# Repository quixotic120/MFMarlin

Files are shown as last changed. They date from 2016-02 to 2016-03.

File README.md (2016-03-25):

# MFMarlin
Marlin 1.1.0 RC3 for Makerfarm Pegasus

**in this configuration software endstops are turned off; as a result you will be able to crash the head very easily if you manually move the print head or incorrectly set offsets. If you do not want it to act this way edit line 404 of configuration.h to be true instead of false**

newest changes: speed has been changed because I changed my stepper drivers. I blew out the stepsticks that came with it because I am dumb and replaced with DRV8825 - trying out 1/32nd stepping for now. Added in second extruder but recently picked up a diamond hotend - added experimental support for CMY color mixing. Untested.

added a ferrite core to the servo signal line and powered with a 7805 rather than using the arduino. Jitter is improved quite a bit but still present unfortunately. Considering building a [noise trap](http://www.sentex.ca/~mec1995/gadgets/noiserx.htm) because I found a hex-schmitt IC in my parts bin; also might add caps to the power and signal lines (see arduino_servo_filters.jpg)

https://github.com/MarlinFirmware/Marlin - I didn't fork because I'm dumb but all the real work is from here; mine is merely a configuration for a 10" Makerfarm pegasus, figured I would share to help anyone else that has a similar setup. I'm also using this document as a collection of what I've done so I can keep track.

This is typically going to be configured for my setup (described below). I'll try to maintain it for as long as possible but no guarantees on that front. I would suggest that if you download this you read over configuration.h at least once - you'll likely at least need to change the bed size and would probably benefit from adding your own PID tunings. If you are using auto bed level you will need to enter the measurements for your machine and if not you should disable it and turn software endstops on.

I have a 10" Pegasus dual extruder with E3Dv6 extruders, graphical LCD, a servo for auto bed leveling (abl), 3mm Borosilicate over bed, SSR on bed for PID control, new bed clips, and some other mods that don't impact the firmware (octopi, cooling for Ramps, lighting, etc). Working fine for me however I do not take any responsibility for you destroying your machine or whatever and no warranty is expressed or implied. Also - I tend to err on the side of slower printing so you may need to play with that a bit for your preferences.

my current slicer settings posted in /slicer as an fff file for simplify3d. If you don't use S3D you can just open it on github; it's basically an XML file. I typically end up messing with the standard stuff, infill/raft/layer height/temperature/etc but the rest is mostly locked in at this point.

Change notes for MFMarlin:
configuration.h

line 73: MB type; I have it set to BOARD_RAMPS_14_EEB - extruder, extruder, bed. Single extruder may want EFB at the end (extruder, fan, bed) or something else depending on what you have connected to D10/9/8, see 

line 78: custom machine name if you want to change the "pegasus ready" text

line 86: define # of extruders. set to 1 currently because I broke my secondary thermistor. D'oh!

thermal settings should be the same unless you've changed thermistors. On that note I've read Makerfarm uses custom thermistor tables but I compared his versus the one in this release and they were essentially identical so thermistortables.h is unchanged; unsure if what I heard was wrong or if this only applies to the prusa i3v

lines 175-178 may have to change for E3Dv6 lite? 

PID:
lines 218-20 are the settings from my extruder with pidautotune, would probably be beneficial to run your own and put in your own values (M303 E0 C8 S210, where E is device (e0 ext 1, e1 ext 2, e-1 bed), C is # cycles, and S is target temp). I see that RC3 has the option to use seperate PID for each extruder, I will likely play with this some more when my replacement thermistor comes

line 246 (#define PIDTEMPBED) - comment this out if you do not use PID for the bed (if you are using the default relay from the kit you should comment this out, I use a Fotek SSR)

lines 270-72 are my bed settings from pidautotune, again suggest you grab your own (M303 E-1 C8 S100)

thermal runaway is on, settings for this have moved to configuration_adv.h - I upped the protection period to 60s because I found myself getting false positives with the PID bed. Consider changing configuration_adv.h line 21 to 40 if you are not. 

back to configuration.h:
346-52: endstop inverting. I have them all as false, colin's has x_max inverted which shouldn't matter as the machine doesn't have max endstops - on that note line 353 is not commented out, comment out to add max endstops 

404 - set to false, set to true if you aren't using abl/are using abl with a second endstop wired in series.

410-415 - my bed limits. If you have the 8" machine this will definitely need to be changed. If you have the default 10 with binder clips you'll probably have to pull it in a bit; I've modified how my glass clamps to the bed to maximize build area. I also place my x and y endstops at x0 y0

420 - filament runout sensor is commented out, not using.

430-50 manual bed leveling is commented out because I'm using abl, uncomment line 434 to add it back into the menu

auto bed level section

457 - comment out to disable ABL

480-83 - box, if you've changed the bed size you'll likely need to change this

489 - # of probe points x 3, set to 3 (probes 9 points)

506-08 - z probe offsets from extruder - [you will need to measure these on your own] (http://zennmaster.com/random-things/auto-bed-leveling-for-the-makerfarm-prusa-i3-part-3-final-setup)

510-517 - z probe behavior, customize to your preference

602-613 - copied from Colin's release. Ensure these values match the ones in your machines config, especially axis_steps_per_unit!

640 - eeprom storage enabled

654-61 - preheat settings. Mine are probably a touch high but they work for my primary filament brand (inland)

LCD - 
if you're using no LCD comment out line 725 (#define REPRAP_DISCOUNT_FULL_GRAPHIC_SMART_CONTROLLER). If you're using the graphic LCD leave as is and install the [u8glib arduino library](https://github.com/olikraus/u8glib)

if you're using the other LCD comment out 725 as above and I believe you uncomment line 715: #define REPRAP_DISCOUNT_SMART_CONTROLLER

RC servo stuff:
comment out line 816 to disable servos

if you are using a servo for abl ensure you set #define SERVO_ENDSTOP_ANGLES on line 826 for your setup

if the servo is unable to complete moves increase servo_activation_delay on line 837, I'm using a towerpro 9g servo so I had to up it a bit. If you notice the servo jerking a bit after it's finished you might need to decrease it. 

other changes:
ultralcd.cpp line 1669 - changed incrementor to += to invert direction of rotary knob on LCD display

bugs found:
random reboot - appears to be a function of using too much at once (e.g. ramping heat WAY up on both extruders and bed while having the carriage move around) and is most likely an issue with my power supply, but still trying to see if I can reproduce it. 
SD sometimes not detected after reboot - every time this has happened reseating the card has fixed the issue. again, trying to reproduce consistently. 

msg me if you find a bug or have questions although I do not guarantee I can help or will respond in a timely manner.

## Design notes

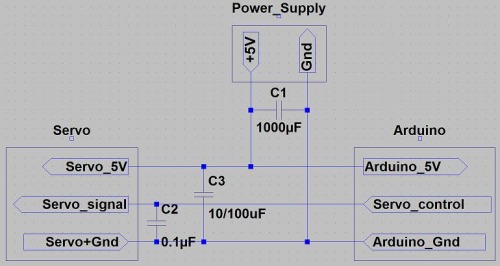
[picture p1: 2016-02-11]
Arduino_Servo_Filters.jpg

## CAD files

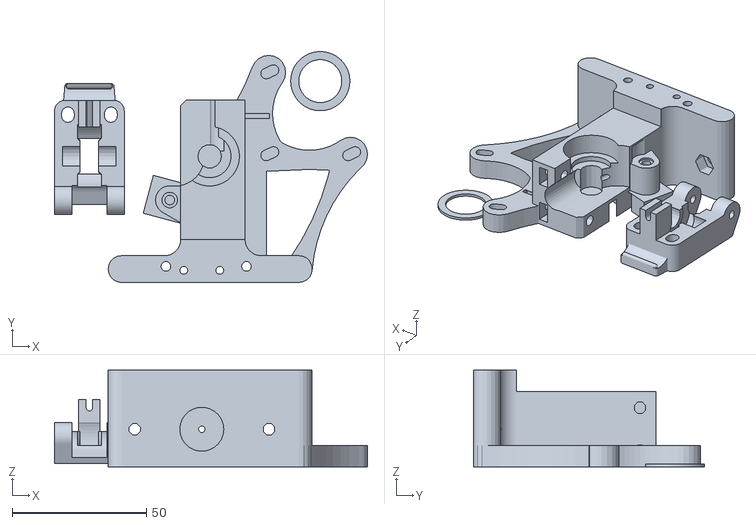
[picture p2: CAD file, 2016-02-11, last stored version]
mods/bowden/orig/ult-gregs-wades-30mm-v1_complete.stl
116.6 x 86.0 x 36.0

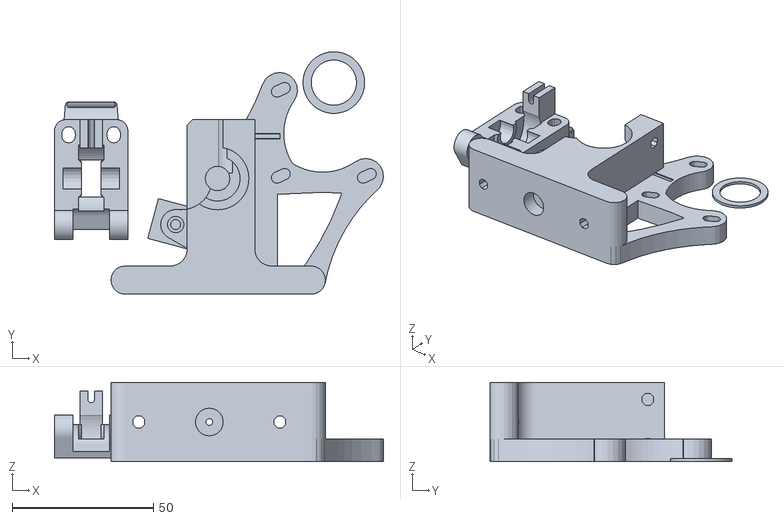
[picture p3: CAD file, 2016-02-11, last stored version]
mods/bowden/bowden mod/ult-gregs-wades-Bowden_base-v1.stl
116.6 x 85.9 x 28.0

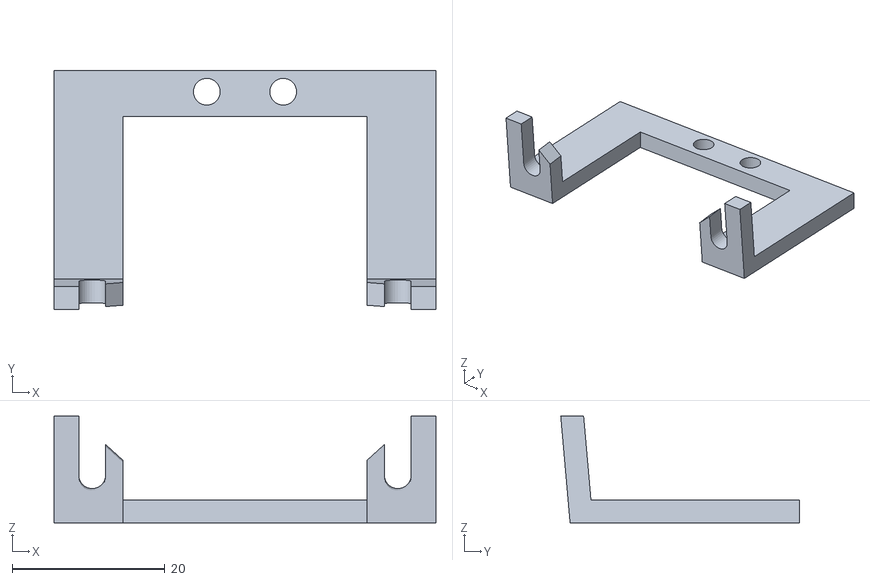
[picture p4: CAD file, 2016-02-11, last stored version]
mods/bowden/e3d mount/Bowden_carriage_clamp_50mmFanbracket.stl
50.0 x 31.2 x 14.0

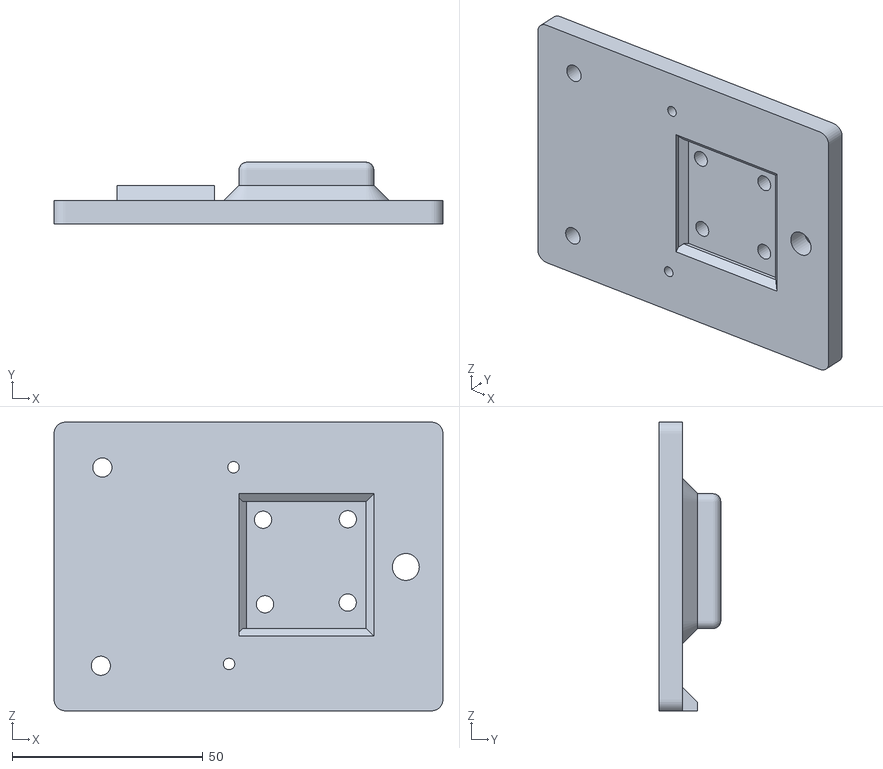
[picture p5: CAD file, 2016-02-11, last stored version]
mods/bowden/e3d mount/E3D_V6_Bowden_mount_with_servo./i3v_Conversion_bracket_1.stl
102.0 x 16.2 x 75.8

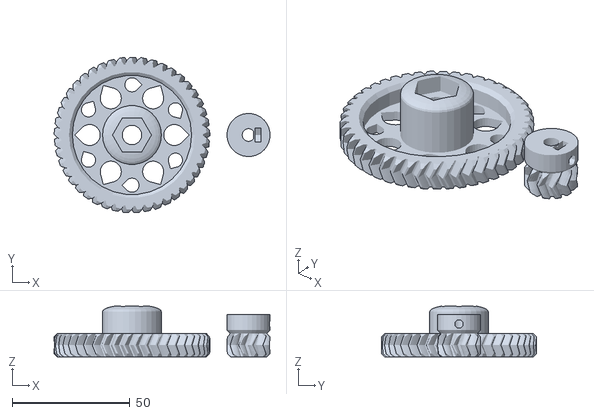
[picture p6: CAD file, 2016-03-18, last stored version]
mods/bowden/flexy mod w: bowden/WadeHerringboneGears.stl
91.7 x 65.9 x 21.6

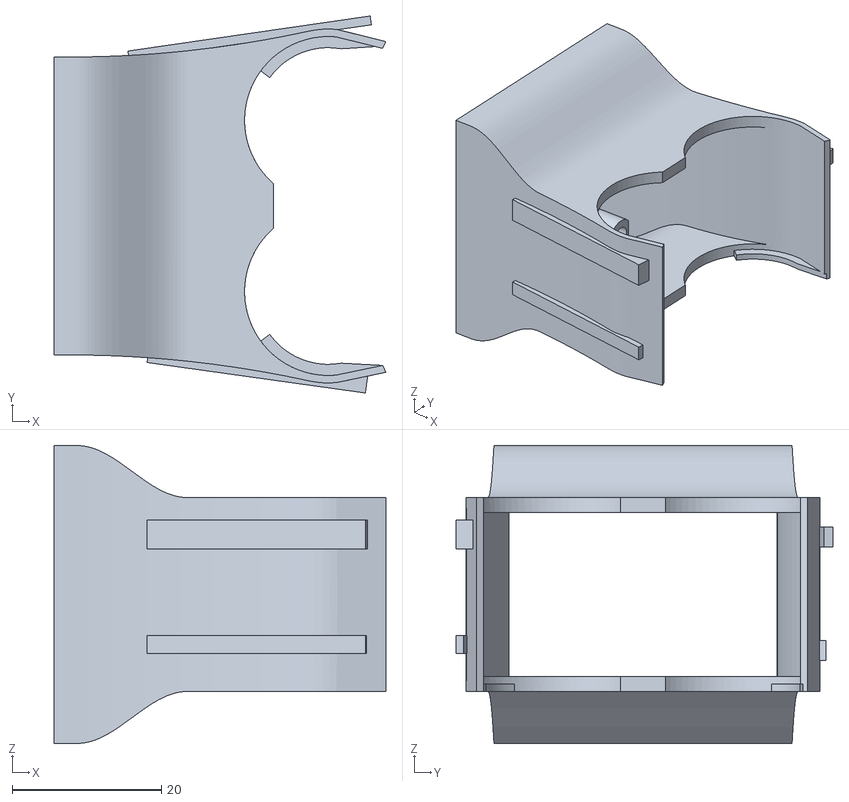
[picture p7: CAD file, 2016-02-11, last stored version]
mods/fan shroud/shroud.stl
44.5 x 50.6 x 40.0

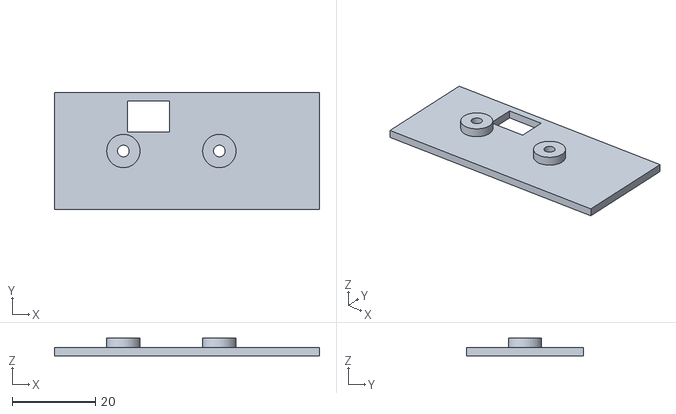
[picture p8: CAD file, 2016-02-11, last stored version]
mods/OrmerodSensorBoard/PrintedPartsForSensorBoard/Insulator-diff-led-dual-nozzle.stl
63.5 x 28.0 x 4.25

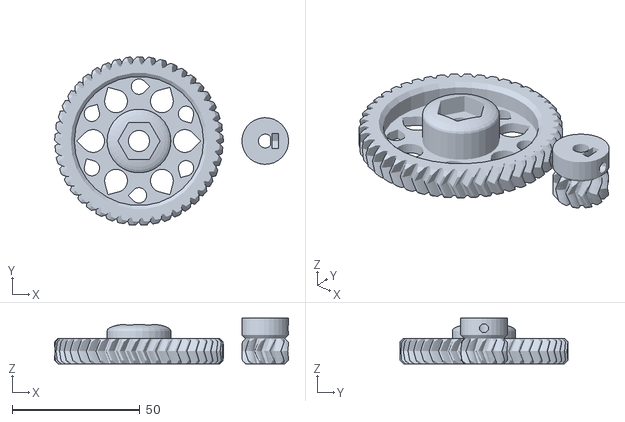
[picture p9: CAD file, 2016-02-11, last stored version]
mods/bowden/bowden mod/WadeHerringboneGears.stl
91.7 x 65.9 x 18.0

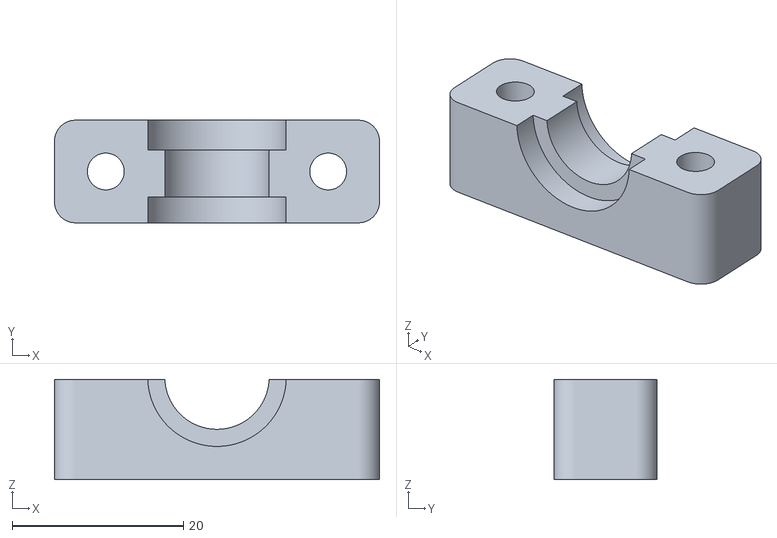
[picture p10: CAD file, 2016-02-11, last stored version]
mods/bowden/e3d mount/Bowden_carriage_clamp.stl
38.0 x 12.0 x 11.8

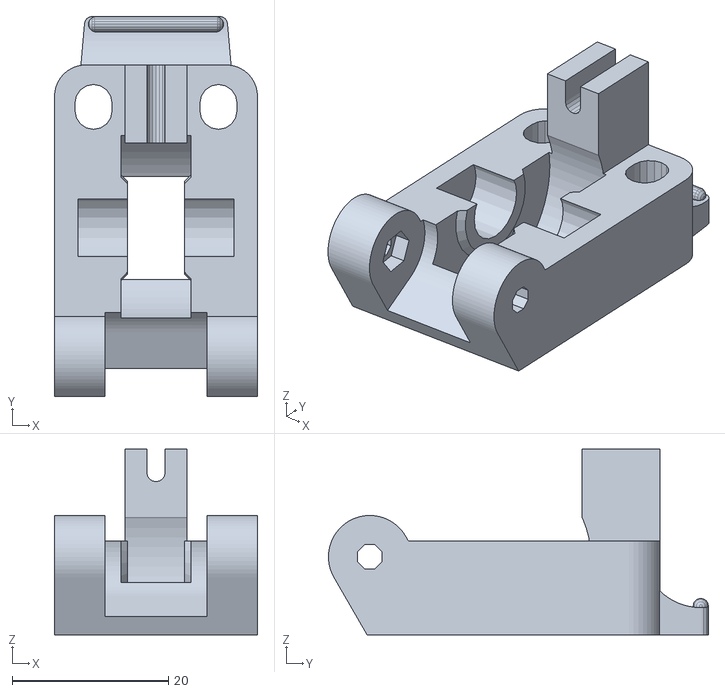
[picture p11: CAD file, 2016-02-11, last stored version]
mods/bowden/orig/ult-gregs-wades-30mm-v1_guidler.stl
26.0 x 48.7 x 23.8

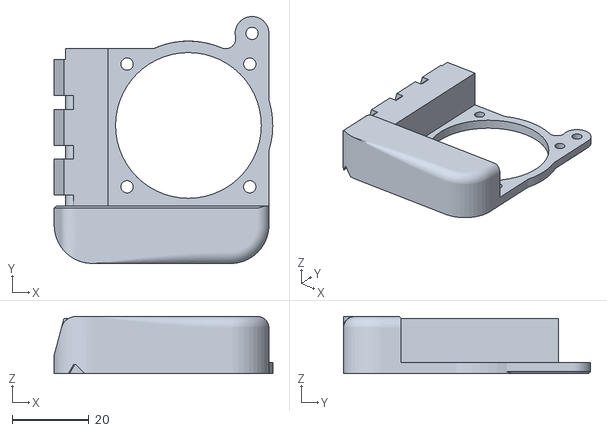
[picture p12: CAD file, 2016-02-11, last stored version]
mods/OrmerodSensorBoard/PrintedPartsForSensorBoard/original-rrp-fan-duct.stl
57.0 x 64.4 x 14.9

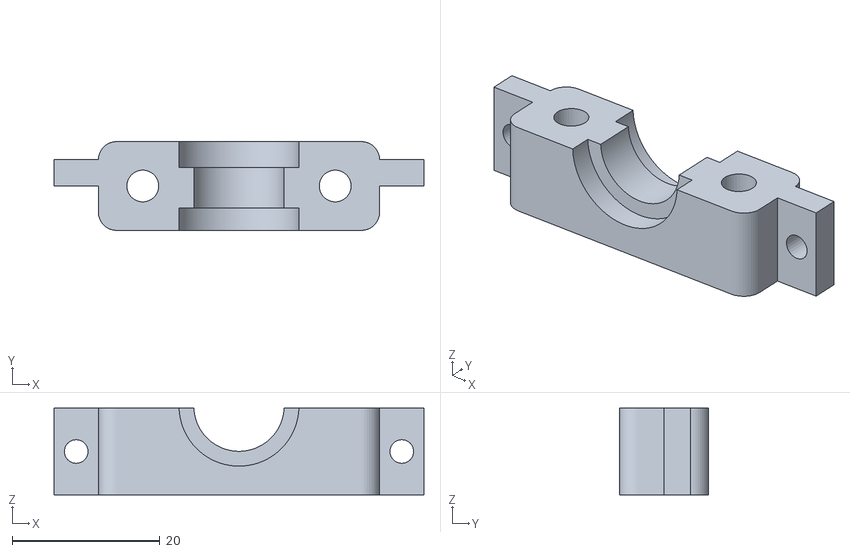
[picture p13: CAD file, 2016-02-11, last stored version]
mods/bowden/e3d mount/Bowden_carriage_clamp_FanMount.stl
50.0 x 12.0 x 11.8

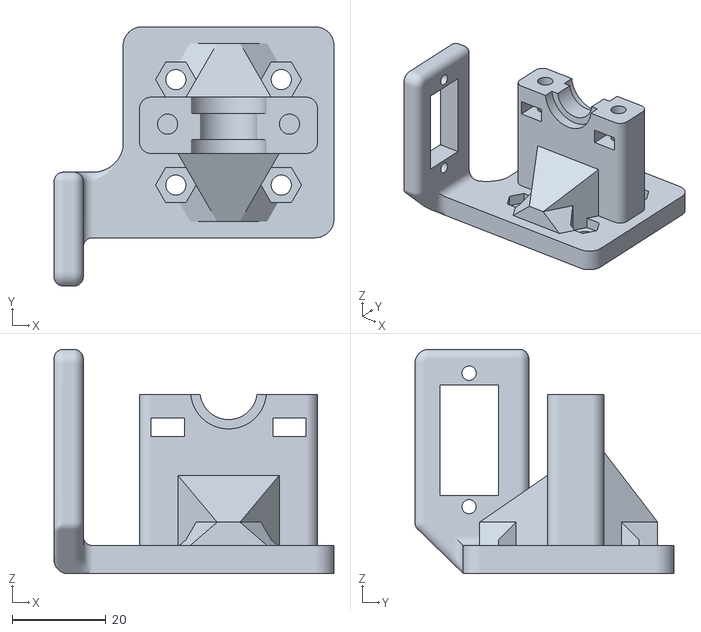
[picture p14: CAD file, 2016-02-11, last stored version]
mods/bowden/e3d mount/E3D_V6_Bowden_mount_with_servo./e3d_bowden_w_servo.stl
59.8 x 55.3 x 47.9

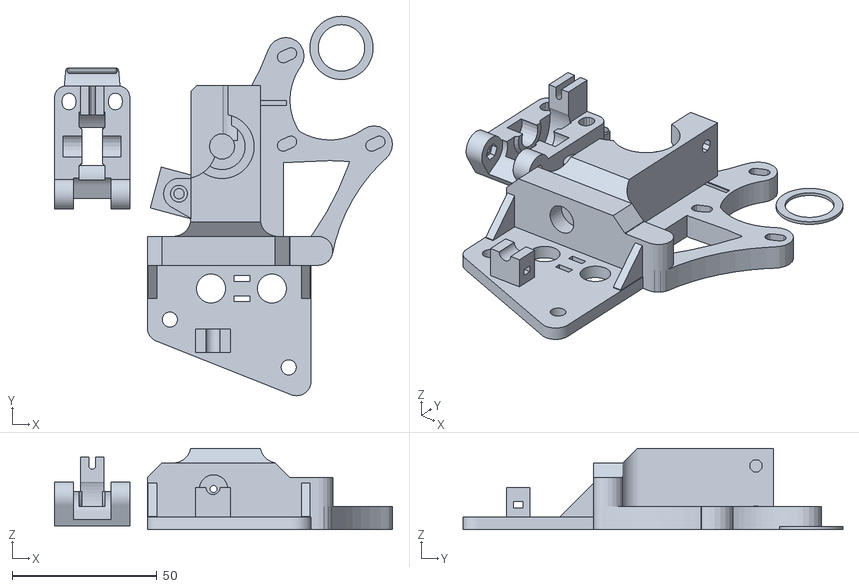
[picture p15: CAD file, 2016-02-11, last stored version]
mods/bowden/bowden mod/ult-gregs-wades-Bowden_bracket-v1.stl
116.6 x 130.9 x 28.0

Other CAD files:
mods/bowden/flexy mod w: bowden/flexy-fixed-gregs-wades.stl
mods/bowden/bowden mod/configuration.scad
mods/bowden/flexy mod w: bowden/configuration.scad
mods/bowden/orig/configuration.scad
mods/OrmerodSensorBoard/PrintedPartsForSensorBoard/BoardHolder-diff-led-dual.scad
mods/OrmerodSensorBoard/PrintedPartsForSensorBoard/BoardHolder-diff-led-mini.scad
mods/OrmerodSensorBoard/PrintedPartsForSensorBoard/BoardHolder-diff-led.scad
mods/OrmerodSensorBoard/PrintedPartsForSensorBoard/BoardHolder-diff-led.stl
mods/OrmerodSensorBoard/PrintedPartsForSensorBoard/BoardHolder.scad
mods/OrmerodSensorBoard/PrintedPartsForSensorBoard/BoardHolder.stl
mods/OrmerodSensorBoard/PrintedPartsForSensorBoard/Insulator-diff-led.scad
mods/OrmerodSensorBoard/PrintedPartsForSensorBoard/Insulator-diff-led.stl
mods/OrmerodSensorBoard/PrintedPartsForSensorBoard/Insulator-for-ultrasonic.scad
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

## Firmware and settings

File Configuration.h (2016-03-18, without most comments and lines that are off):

#define CONFIGURATION_H
#include "boards.h"
#include "macros.h"
#if ENABLED(USE_AUTOMATIC_VERSIONING)
  #include "_Version.h"
#else
  #include "Default_Version.h"
#endif
#define STRING_CONFIG_H_AUTHOR ("Jon, Makerfarm Pegasus Dual 10\" 1.1.0 RC3") // Who made the changes.
#define SHOW_BOOTSCREEN
#define STRING_SPLASH_LINE1 SHORT_BUILD_VERSION // will be shown during bootup in line 1
#define SERIAL_PORT 0
#define BAUDRATE 115200
  #define MOTHERBOARD 44
#define CUSTOM_MACHINE_NAME "Pegasus"
#define MACHINE_UUID "9831ee20-f544-40ec-9450-58e42773382e"
#define EXTRUDERS 1
#define EXTRUDER_OFFSET_X {0.0, 25.30} // (in mm) for each extruder, offset of the hotend on the X axis
#define EXTRUDER_OFFSET_Y {0.0, -1.00}  // (in mm) for each extruder, offset of the hotend on the Y axis
#define POWER_SUPPLY 1
#define TEMP_SENSOR_0 52
#define TEMP_SENSOR_1 52
#define TEMP_SENSOR_2 0
#define TEMP_SENSOR_3 0
#define TEMP_SENSOR_BED 52
#define MAX_REDUNDANT_TEMP_SENSOR_DIFF 10
#define TEMP_RESIDENCY_TIME 10  // (seconds)
#define TEMP_HYSTERESIS 3       // (degC) range of +/- temperatures considered "close" to the target one
#define TEMP_WINDOW     1       // (degC) Window around target to start the residency timer x degC early.
#define HEATER_0_MINTEMP 5
#define HEATER_1_MINTEMP 5
#define HEATER_2_MINTEMP 5
#define HEATER_3_MINTEMP 5
#define BED_MINTEMP 5
#define HEATER_0_MAXTEMP 275
#define HEATER_1_MAXTEMP 275
#define HEATER_2_MAXTEMP 275
#define HEATER_3_MAXTEMP 275
#define BED_MAXTEMP 150
#define PIDTEMP
#define BANG_MAX 255 // limits current to nozzle while in bang-bang mode; 255=full current
#define PID_MAX BANG_MAX // limits current to nozzle while PID is active (see PID_FUNCTIONAL_RANGE below); 255=full current
  #define PID_PARAMS_PER_EXTRUDER // Uses separate PID parameters for each extruder (useful for mismatched extruders)
  #define PID_FUNCTIONAL_RANGE 10 // If the temperature difference between the target temperature and the actual temperature
  #define PID_INTEGRAL_DRIVE_MAX PID_MAX  //limit for the integral term
  #define K1 0.95 //smoothing factor within the PID
  #define  DEFAULT_Kp 34.24
  #define  DEFAULT_Ki 3.80
  #define  DEFAULT_Kd 77.18
#define PIDTEMPBED
#define MAX_BED_POWER 255 // limits duty cycle to bed; 255=full current
  #define PID_BED_INTEGRAL_DRIVE_MAX MAX_BED_POWER //limit for the integral term
  #define  DEFAULT_bedKp 209.84
  #define  DEFAULT_bedKi 41.05
  #define  DEFAULT_bedKd 268.18
#define PREVENT_DANGEROUS_EXTRUDE
#define PREVENT_LENGTHY_EXTRUDE
#define EXTRUDE_MINTEMP 170
#define EXTRUDE_MAXLENGTH (X_MAX_LENGTH+Y_MAX_LENGTH) //prevent extrusion of very large distances.
#define THERMAL_PROTECTION_HOTENDS // Enable thermal protection for all extruders
#define THERMAL_PROTECTION_BED     // Enable thermal protection for the heated bed
#define ENDSTOPPULLUPS // Comment this out (using // at the start of the line) to disable the endstop pullup resistors
const bool X_MIN_ENDSTOP_INVERTING = false; // set to true to invert the logic of the endstop.
const bool Y_MIN_ENDSTOP_INVERTING = false; // set to true to invert the logic of the endstop.
const bool Z_MIN_ENDSTOP_INVERTING = false; // set to true to invert the logic of the endstop.
const bool X_MAX_ENDSTOP_INVERTING = false; // set to true to invert the logic of the endstop.
const bool Y_MAX_ENDSTOP_INVERTING = false; // set to true to invert the logic of the endstop.
const bool Z_MAX_ENDSTOP_INVERTING = false; // set to true to invert the logic of the endstop.
const bool Z_MIN_PROBE_ENDSTOP_INVERTING = false; // set to true to invert the logic of the endstop.
#define DISABLE_MAX_ENDSTOPS
#define X_ENABLE_ON 0
#define Y_ENABLE_ON 0
#define Z_ENABLE_ON 0
#define E_ENABLE_ON 0 // For all extruders
#define DISABLE_X false
#define DISABLE_Y false
#define DISABLE_Z false
#define DISABLE_E false // For all extruders
#define DISABLE_INACTIVE_EXTRUDER true //disable only inactive extruders and keep active extruder enabled
#define INVERT_X_DIR true
#define INVERT_Y_DIR false
#define INVERT_Z_DIR false
#define INVERT_E0_DIR false
#define INVERT_E1_DIR false
#define INVERT_E2_DIR false
#define INVERT_E3_DIR false
#define X_HOME_DIR -1
#define Y_HOME_DIR -1
#define Z_HOME_DIR -1
#define min_software_endstops false // If true, axis won't move to coordinates less than HOME_POS.
#define max_software_endstops true  // If true, axis won't move to coordinates greater than the defined lengths below.
#define X_MIN_POS 0
#define Y_MIN_POS 0
#define Z_MIN_POS 0
#define X_MAX_POS 205
#define Y_MAX_POS 234
#define Z_MAX_POS 240
#define AUTO_BED_LEVELING_FEATURE // Delete the comment to enable (remove // at the start of the line)
#define Z_MIN_PROBE_REPEATABILITY_TEST  // If not commented out, Z-Probe Repeatability test will be included if Auto Bed Leveling is Enabled.
  #define AUTO_BED_LEVELING_GRID
    #define LEFT_PROBE_BED_POSITION 20
    #define RIGHT_PROBE_BED_POSITION 161
    #define FRONT_PROBE_BED_POSITION 20
    #define BACK_PROBE_BED_POSITION 200
    #define MIN_PROBE_EDGE 5 // The Z probe minimum square sides can be no smaller than this.
    #define AUTO_BED_LEVELING_GRID_POINTS 3
  #define X_PROBE_OFFSET_FROM_EXTRUDER -44     // Z probe to nozzle X offset: -left  +right
  #define Y_PROBE_OFFSET_FROM_EXTRUDER -12    // Z probe to nozzle Y offset: -front +behind
  #define Z_PROBE_OFFSET_FROM_EXTRUDER -7.8  // Z probe to nozzle Z offset: -below (always!)
  #define Z_RAISE_BEFORE_HOMING 15     // (in mm) Raise Z axis before homing (G28) for Z probe clearance.
  #define XY_TRAVEL_SPEED 3000         // X and Y axis travel speed between probes, in mm/min.
  #define Z_RAISE_BEFORE_PROBING 20  // How much the Z axis will be raised before traveling to the first probing point.
  #define Z_RAISE_BETWEEN_PROBINGS 20 // How much the Z axis will be raised when traveling from between next probing points.
  #define Z_RAISE_AFTER_PROBING 20   // How much the Z axis will be raised after the last probing point.
  #define Z_SAFE_HOMING   // This feature is meant to avoid Z homing with Z probe outside the bed area.
    #define Z_SAFE_HOMING_X_POINT ((X_MIN_POS + X_MAX_POS) / 2)    // X point for Z homing when homing all axis (G28).
    #define Z_SAFE_HOMING_Y_POINT ((Y_MIN_POS + Y_MAX_POS) / 2)    // Y point for Z homing when homing all axis (G28).
#define HOMING_FEEDRATE {50*60, 50*60, 200, 0}  // set the homing speeds (mm/min)
#define DEFAULT_AXIS_STEPS_PER_UNIT   {160.38,160.38,5120,180}  // default steps per unit for Ultimaker
#define DEFAULT_MAX_FEEDRATE          {500, 500, 2, 50}    // (mm/sec)
#define DEFAULT_MAX_ACCELERATION      {3000,3000,5,3000}    // X, Y, Z, E maximum start speed for accelerated moves. E default values are good for Skeinforge 40+, for older versions raise them a lot.
#define DEFAULT_ACCELERATION          500    // X, Y, Z and E acceleration in mm/s^2 for printing moves
#define DEFAULT_RETRACT_ACCELERATION  500    // E acceleration in mm/s^2 for retracts
#define DEFAULT_TRAVEL_ACCELERATION   500    // X, Y, Z acceleration in mm/s^2 for travel (non printing) moves
#define DEFAULT_XYJERK                20.0    // (mm/sec)
#define DEFAULT_ZJERK                 0.4     // (mm/sec)
#define DEFAULT_EJERK                 5.0    // (mm/sec)
#define CUSTOM_M_CODES
    #define CUSTOM_M_CODE_SET_Z_PROBE_OFFSET 851
    #define Z_PROBE_OFFSET_RANGE_MIN -20
    #define Z_PROBE_OFFSET_RANGE_MAX 20
#define EEPROM_SETTINGS
  #define EEPROM_CHITCHAT // Please keep turned on if you can.
#define PLA_PREHEAT_HOTEND_TEMP 205
#define PLA_PREHEAT_HPB_TEMP 45
#define PLA_PREHEAT_FAN_SPEED 0   // Insert Value between 0 and 255
#define ABS_PREHEAT_HOTEND_TEMP 250
#define ABS_PREHEAT_HPB_TEMP 100
#define ABS_PREHEAT_FAN_SPEED 0   // Insert Value between 0 and 255
#define LANGUAGE_INCLUDE GENERATE_LANGUAGE_INCLUDE(en)
  #define DISPLAY_CHARSET_HD44780_JAPAN        // this is the most common hardware
#define SDSUPPORT // Enable SD Card Support in Hardware Console
#define REPRAP_DISCOUNT_FULL_GRAPHIC_SMART_CONTROLLER
#define SOFT_PWM_SCALE 0
#define NUM_SERVOS 3 // Servo index starts with 0 for M280 command
#define X_ENDSTOP_SERVO_NR -1
#define Y_ENDSTOP_SERVO_NR -1
#define Z_ENDSTOP_SERVO_NR 0
#define SERVO_ENDSTOP_ANGLES {{0,0}, {0,0}, {93,0}} // X,Y,Z Axis Extend and Retract angles
#define DEACTIVATE_SERVOS_AFTER_MOVE
  #define SERVO_DEACTIVATION_DELAY 500
#define FILAMENT_SENSOR_EXTRUDER_NUM 0   //The number of the extruder that has the filament sensor (0,1,2)
#define MEASUREMENT_DELAY_CM        14   //measurement delay in cm.  This is the distance from filament sensor to middle of barrel
#define DEFAULT_NOMINAL_FILAMENT_DIA 3.00  //Enter the diameter (in mm) of the filament generally used (3.0 mm or 1.75 mm) - this is then used in the slicer software.  Used for sensor reading validation
#define MEASURED_UPPER_LIMIT         3.30  //upper limit factor used for sensor reading validation in mm
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

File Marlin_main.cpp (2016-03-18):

/**
 * Marlin Firmware
 *
 * Based on Sprinter and grbl.
 * Copyright (C) 2011 Camiel Gubbels / Erik van der Zalm
 *
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
 * About Marlin
 *
 * This firmware is a mashup between Sprinter and grbl.
 *  - https://github.com/kliment/Sprinter
 *  - https://github.com/simen/grbl/tree
 *
 * It has preliminary support for Matthew Roberts advance algorithm
 *  - http://reprap.org/pipermail/reprap-dev/2011-May/003323.html
 */

#include "Marlin.h"

#if ENABLED(AUTO_BED_LEVELING_FEATURE)
  #include "vector_3.h"
  #if ENABLED(AUTO_BED_LEVELING_GRID)
    #include "qr_solve.h"
  #endif
#endif // AUTO_BED_LEVELING_FEATURE

#if ENABLED(MESH_BED_LEVELING)
  #include "mesh_bed_leveling.h"
#endif

#include "ultralcd.h"
#include "planner.h"
#include "stepper.h"
#include "temperature.h"
#include "cardreader.h"
#include "configuration_store.h"
#include "language.h"
#include "pins_arduino.h"
#include "math.h"
#include "buzzer.h"

#if ENABLED(USE_WATCHDOG)
  #include "watchdog.h"
#endif

#if ENABLED(BLINKM)
  #include "blinkm.h"
  #include "Wire.h"
#endif

#if HAS_SERVOS
  #include "servo.h"
#endif

#if HAS_DIGIPOTSS
  #include <SPI.h>
#endif

// The external gCode implementations
//#include "gCodes.h"

/**
 * Look here for descriptions of G-codes:
 *  - http://linuxcnc.org/handbook/gcode/g-code.html
 *  - http://objects.reprap.org/wiki/Mendel_User_Manual:_RepRapGCodes
 *
 * Help us document these G-codes online:
 *  - https://github.com/MarlinFirmware/MarlinDev/wiki/G-Code-in-Marlin
 *  - http://reprap.org/wiki/G-code
 *
 * -----------------
 * Implemented Codes
 * -----------------
 *
 * "G" Codes
 *
 * G0  -> G1
 * G1  - Coordinated Movement X Y Z E
 * G2  - CW ARC
 * G3  - CCW ARC
 * G4  - Dwell S<seconds> or P<milliseconds>
 * G10 - retract filament according to settings of M207
 * G11 - retract recover filament according to settings of M208
 * G28 - Home one or more axes
 * G29 - Detailed Z probe, probes the bed at 3 or more points.  Will fail if you haven't homed yet.
 * G30 - Single Z probe, probes bed at current XY location.
 * G31 - Dock sled (Z_PROBE_SLED only)
 * G32 - Undock sled (Z_PROBE_SLED only)
 * G90 - Use Absolute Coordinates
 * G91 - Use Relative Coordinates
 * G92 - Set current position to coordinates given
 *
 * "M" Codes
 *
 * M0   - Unconditional stop - Wait for user to press a button on the LCD (Only if ULTRA_LCD is enabled)
 * M1   - Same as M0
 * M17  - Enable/Power all stepper motors
 * M18  - Disable all stepper motors; same as M84
 * M20  - List SD card
 * M21  - Init SD card
 * M22  - Release SD card
 * M23  - Select SD file (M23 filename.g)
 * M24  - Start/resume SD print
 * M25  - Pause SD print
 * M26  - Set SD position in bytes (M26 S12345)
 * M27  - Report SD print status
 * M28  - Start SD write (M28 filename.g)
 * M29  - Stop SD write
 * M30  - Delete file from SD (M30 filename.g)
 * M31  - Output time since last M109 or SD card start to serial
 * M32  - Select file and start SD print (Can be used _while_ printing from SD card files):
 *        syntax "M32 /path/filename#", or "M32 S<startpos bytes> !filename#"
 *        Call gcode file : "M32 P !filename#" and return to caller file after finishing (similar to #include).
 *        The '#' is necessary when calling from within sd files, as it stops buffer prereading
 * M33  - Get the longname version of a path
 * M42  - Change pin status via gcode Use M42 Px Sy to set pin x to value y, when omitting Px the onboard led will be used.
 * M48  - Measure Z_Probe repeatability. M48 [P # of points] [X position] [Y position] [V_erboseness #] [E_ngage Probe] [L # of legs of travel]
 * M80  - Turn on Power Supply
 * M81  - Turn off Power Supply
 * M82  - Set E codes absolute (default)
 * M83  - Set E codes relative while in Absolute Coordinates (G90) mode
 * M84  - Disable steppers until next move,
 *        or use S<seconds> to specify an inactivity timeout, after which the steppers will be disabled.  S0 to disable the timeout.
 * M85  - Set inactivity shutdown timer with parameter S<seconds>. To disable set zero (default)
 * M92  - Set axis_steps_per_unit - same syntax as G92
 * M104 - Set extruder target temp
 * M105 - Read current temp
 * M106 - Fan on
 * M107 - Fan off
 * M109 - Sxxx Wait for extruder current temp to reach target temp. Waits only when heating
 *        Rxxx Wait for extruder current temp to reach target temp. Waits when heating and cooling
 *        IF AUTOTEMP is enabled, S<mintemp> B<maxtemp> F<factor>. Exit autotemp by any M109 without F
 * M110 - Set the current line number
 * M111 - Set debug flags with S<mask>. See flag bits defined in Marlin.h.
 * M112 - Emergency stop
 * M114 - Output current position to serial port
 * M115 - Capabilities string
 * M117 - Display a message on the controller screen
 * M119 - Output Endstop status to serial port
 * M120 - Enable endstop detection
 * M121 - Disable endstop detection
 * M126 - Solenoid Air Valve Open (BariCUDA support by jmil)
 * M127 - Solenoid Air Valve Closed (BariCUDA vent to atmospheric pressure by jmil)
 * M128 - EtoP Open (BariCUDA EtoP = electricity to air pressure transducer by jmil)
 * M129 - EtoP Closed (BariCUDA EtoP = electricity to air pressure transducer by jmil)
 * M140 - Set bed target temp
 * M145 - Set the heatup state H<hotend> B<bed> F<fan speed> for S<material> (0=PLA, 1=ABS)
 * M150 - Set BlinkM Color Output R: Red<0-255> U(!): Green<0-255> B: Blue<0-255> over i2c, G for green does not work.
 * M163 - Set a single proportion for a mixing extruder. Requires MIXING_EXTRUDER_FEATURE.
 * M164 - Save the mix as a virtual extruder. Requires MIXING_EXTRUDER_FEATURE and MIXING_VIRTUAL_TOOLS.
 * M165 - Set the proportions for a mixing extruder. Use parameters ABCDHI to set the mixing factors. Requires MIXING_EXTRUDER_FEATURE.
 * M190 - Sxxx Wait for bed current temp to reach target temp. Waits only when heating
 *        Rxxx Wait for bed current temp to reach target temp. Waits when heating and cooling
 * M200 - set filament diameter and set E axis units to cubic millimeters (use S0 to set back to millimeters).:D<millimeters>-
 * M201 - Set max acceleration in units/s^2 for print moves (M201 X1000 Y1000)
 * M202 - Set max acceleration in units/s^2 for travel moves (M202 X1000 Y1000) Unused in Marlin!!
 * M203 - Set maximum feedrate that your machine can sustain (M203 X200 Y200 Z300 E10000) in mm/sec
 * M204 - Set default acceleration: P for Printing moves, R for Retract only (no X, Y, Z) moves and T for Travel (non printing) moves (ex. M204 P800 T3000 R9000) in mm/sec^2
 * M205 -  advanced settings:  minimum travel speed S=while printing T=travel only,  B=minimum segment time X= maximum xy jerk, Z=maximum Z jerk, E=maximum E jerk
 * M206 - Set additional homing offset
 * M207 - Set retract length S[positive mm] F[feedrate mm/min] Z[additional zlift/hop], stays in mm regardless of M200 setting
 * M208 - Set recover=unretract length S[positive mm surplus to the M207 S*] F[feedrate mm/min]
 * M209 - S<1=true/0=false> enable automatic retract detect if the slicer did not support G10/11: every normal extrude-only move will be classified as retract depending on the direction.
 * M218 - Set hotend offset (in mm): T<extruder_number> X<offset_on_X> Y<offset_on_Y>
 * M220 - Set speed factor override percentage: S<factor in percent>
 * M221 - Set extrude factor override percentage: S<factor in percent>
 * M226 - Wait until the specified pin reaches the state required: P<pin number> S<pin state>
 * M240 - Trigger a camera to take a photograph
 * M250 - Set LCD contrast C<contrast value> (value 0..63)
 * M280 - Set servo position absolute. P: servo index, S: angle or microseconds
 * M300 - Play beep sound S<frequency Hz> P<duration ms>
 * M301 - Set PID parameters P I and D
 * M302 - Allow cold extrudes, or set the minimum extrude S<temperature>.
 * M303 - PID relay autotune S<temperature> sets the target temperature. (default target temperature = 150C)
 * M304 - Set bed PID parameters P I and D
 * M380 - Activate solenoid on active extruder
 * M381 - Disable all solenoids
 * M400 - Finish all moves
 * M401 - Lower Z probe if present
 * M402 - Raise Z probe if present
 * M404 - N<dia in mm> Enter the nominal filament width (3mm, 1.75mm ) or will display nominal filament width without parameters
 * M405 - Turn on Filament Sensor extrusion control.  Optional D<delay in cm> to set delay in centimeters between sensor and extruder
 * M406 - Turn off Filament Sensor extrusion control
 * M407 - Display measured filament diameter
 * M410 - Quickstop. Abort all the planned moves
 * M420 - Enable/Disable Mesh Leveling (with current values) S1=enable S0=disable
 * M421 - Set a single Z coordinate in the Mesh Leveling grid. X<mm> Y<mm> Z<mm>
 * M428 - Set the home_offset logically based on the current_position
 * M500 - Store parameters in EEPROM
 * M501 - Read parameters from EEPROM (if you need reset them after you changed them temporarily).
 * M502 - Revert to the default "factory settings". You still need to store them in EEPROM afterwards if you want to.
 * M503 - Print the current settings (from memory not from EEPROM). Use S0 to leave off headings.
 * M540 - Use S[0|1] to enable or disable the stop SD card print on endstop hit (requires ABORT_ON_ENDSTOP_HIT_FEATURE_ENABLED)
 * M600 - Pause for filament change X[pos] Y[pos] Z[relative lift] E[initial retract] L[later retract distance for removal]
 * M665 - Set delta configurations: L<diagonal rod> R<delta radius> S<segments/s>
 * M666 - Set delta endstop adjustment
 * M605 - Set dual x-carriage movement mode: S<mode> [ X<duplication x-offset> R<duplication temp offset> ]
 * M907 - Set digital trimpot motor current using axis codes.
 * M908 - Control digital trimpot directly.
 * M350 - Set microstepping mode.
 * M351 - Toggle MS1 MS2 pins directly.
 *
 * ************ SCARA Specific - This can change to suit future G-code regulations
 * M360 - SCARA calibration: Move to cal-position ThetaA (0 deg calibration)
 * M361 - SCARA calibration: Move to cal-position ThetaB (90 deg calibration - steps per degree)
 * M362 - SCARA calibration: Move to cal-position PsiA (0 deg calibration)
 * M363 - SCARA calibration: Move to cal-position PsiB (90 deg calibration - steps per degree)
 * M364 - SCARA calibration: Move to cal-position PSIC (90 deg to Theta calibration position)
 * M365 - SCARA calibration: Scaling factor, X, Y, Z axis
 * ************* SCARA End ***************
 *
 * ************ Custom codes - This can change to suit future G-code regulations
 * M100 - Watch Free Memory (For Debugging Only)
 * M851 - Set Z probe's Z offset (mm above extruder -- The value will always be negative)


 * M928 - Start SD logging (M928 filename.g) - ended by M29
 * M999 - Restart after being stopped by error
 *
 * "T" Codes
 *
 * T0-T3 - Select a tool by index (usually an extruder) [ F<mm/min> ]
 *
 */

#if ENABLED(M100_FREE_MEMORY_WATCHER)
  void gcode_M100();
#endif

#if ENABLED(SDSUPPORT)
  CardReader card;
#endif

bool Running = true;

uint8_t marlin_debug_flags = DEBUG_INFO | DEBUG_ERRORS;

static float feedrate = 1500.0, saved_feedrate;
float current_position[NUM_AXIS] = { 0.0 };
static float destination[NUM_AXIS] = { 0.0 };
bool axis_known_position[3] = { false };

static long gcode_N, gcode_LastN, Stopped_gcode_LastN = 0;

static char* current_command, *current_command_args;
static int cmd_queue_index_r = 0;
static int cmd_queue_index_w = 0;
static int commands_in_queue = 0;
static char command_queue[BUFSIZE][MAX_CMD_SIZE];

const float homing_feedrate[] = HOMING_FEEDRATE;
bool axis_relative_modes[] = AXIS_RELATIVE_MODES;
int feedrate_multiplier = 100; //100->1 200->2
int saved_feedrate_multiplier;
int extruder_multiplier[EXTRUDERS] = ARRAY_BY_EXTRUDERS1(100);
bool volumetric_enabled = false;
float filament_size[EXTRUDERS] = ARRAY_BY_EXTRUDERS1(DEFAULT_NOMINAL_FILAMENT_DIA);
float volumetric_multiplier[EXTRUDERS] = ARRAY_BY_EXTRUDERS1(1.0);
float home_offset[3] = { 0 };
float min_pos[3] = { X_MIN_POS, Y_MIN_POS, Z_MIN_POS };
float max_pos[3] = { X_MAX_POS, Y_MAX_POS, Z_MAX_POS };

uint8_t active_extruder = 0;
int fanSpeed = 0;
bool cancel_heatup = false;

const char errormagic[] PROGMEM = "Error:";
const char echomagic[] PROGMEM = "echo:";
const char axis_codes[NUM_AXIS] = {'X', 'Y', 'Z', 'E'};

static bool relative_mode = false;  //Determines Absolute or Relative Coordinates
static char serial_char;
static int serial_count = 0;
static boolean comment_mode = false;
static char* seen_pointer; ///< A pointer to find chars in the command string (X, Y, Z, E, etc.)
const char* queued_commands_P = NULL; /* pointer to the current line in the active sequence of commands, or NULL when none */
const int sensitive_pins[] = SENSITIVE_PINS; ///< Sensitive pin list for M42
// Inactivity shutdown
millis_t previous_cmd_ms = 0;
static millis_t max_inactive_time = 0;
static millis_t stepper_inactive_time = DEFAULT_STEPPER_DEACTIVE_TIME * 1000L;
millis_t print_job_start_ms = 0; ///< Print job start time
millis_t print_job_stop_ms = 0;  ///< Print job stop time
static uint8_t target_extruder;
bool target_direction;
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
void loop() {
  if (commands_in_queue < BUFSIZE - 1) get_command();

  #if ENABLED(SDSUPPORT)
    card.checkautostart(false);
  #endif

  if (commands_in_queue) {

    #if ENABLED(SDSUPPORT)

      if (card.saving) {
        char* command = command_queue[cmd_queue_index_r];
        if (strstr_P(command, PSTR("M29"))) {
          // M29 closes the file
          card.closefile();
          SERIAL_PROTOCOLLNPGM(MSG_FILE_SAVED);
        }
        else {
          // Write the string from the read buffer to SD
          card.write_command(command);
          if (card.logging)
            process_next_command(); // The card is saving because it's logging
          else
            SERIAL_PROTOCOLLNPGM(MSG_OK);
        }
      }
      else
        process_next_command();

    #else

      process_next_command();

    #endif // SDSUPPORT

    commands_in_queue--;
    cmd_queue_index_r = (cmd_queue_index_r + 1) % BUFSIZE;
  }
  checkHitEndstops();
  idle();
}

void gcode_line_error(const char* err, bool doFlush = true) {
  SERIAL_ERROR_START;
  serialprintPGM(err);
  SERIAL_ERRORLN(gcode_LastN);
  //Serial.println(gcode_N);
  if (doFlush) FlushSerialRequestResend();
  serial_count = 0;
}

/**
 * Add to the circular command queue the next command from:
 *  - The command-injection queue (queued_commands_P)
 *  - The active serial input (usually USB)
 *  - The SD card file being actively printed
 */
void get_command() {

  if (drain_queued_commands_P()) return; // priority is given to non-serial commands

  #if ENABLED(NO_TIMEOUTS)
    static millis_t last_command_time = 0;
    millis_t ms = millis();

    if (!MYSERIAL.available() && commands_in_queue == 0 && ms - last_command_time > NO_TIMEOUTS) {
      SERIAL_ECHOLNPGM(MSG_WAIT);
      last_command_time = ms;
    }
  #endif

  //
  // Loop while serial characters are incoming and the queue is not full
  //
  while (commands_in_queue < BUFSIZE && MYSERIAL.available() > 0) {

    #if ENABLED(NO_TIMEOUTS)
      last_command_time = ms;
    #endif

    serial_char = MYSERIAL.read();

    //
    // If the character ends the line, or the line is full...
    //
    if (serial_char == '\n' || serial_char == '\r' || serial_count >= MAX_CMD_SIZE - 1) {

      // end of line == end of comment
      comment_mode = false;

      if (!serial_count) return; // empty lines just exit

      char* command = command_queue[cmd_queue_index_w];
      command[serial_count] = 0; // terminate string

      // this item in the queue is not from sd
      #if ENABLED(SDSUPPORT)
        fromsd[cmd_queue_index_w] = false;
      #endif

      while (*command == ' ') command++; // skip any leading spaces
      char* npos = (*command == 'N') ? command : NULL; // Require the N parameter to start the line
      char* apos = strchr(command, '*');

      if (npos) {

        boolean M110 = strstr_P(command, PSTR("M110")) != NULL;

        if (M110) {
          char* n2pos = strchr(command + 4, 'N');
          if (n2pos) npos = n2pos;
        }

        gcode_N = strtol(npos + 1, NULL, 10);

        if (gcode_N != gcode_LastN + 1 && !M110) {
          gcode_line_error(PSTR(MSG_ERR_LINE_NO));
          return;
        }

        if (apos) {
          byte checksum = 0, count = 0;
          while (command[count] != '*') checksum ^= command[count++];

          if (strtol(apos + 1, NULL, 10) != checksum) {
            gcode_line_error(PSTR(MSG_ERR_CHECKSUM_MISMATCH));
            return;
          }
          // if no errors, continue parsing
        }
        else if (npos == command) {
          gcode_line_error(PSTR(MSG_ERR_NO_CHECKSUM));
          return;
        }

        gcode_LastN = gcode_N;
        // if no errors, continue parsing
      }
      else if (apos) { // No '*' without 'N'
        gcode_line_error(PSTR(MSG_ERR_NO_LINENUMBER_WITH_CHECKSUM), false);
        return;
      }

      // Movement commands alert when stopped
      if (IsStopped()) {
        char* gpos = strchr(command, 'G');
        if (gpos) {
          int codenum = strtol(gpos + 1, NULL, 10);
          switch (codenum) {
            case 0:
            case 1:
            case 2:
            case 3:
              SERIAL_ERRORLNPGM(MSG_ERR_STOPPED);
              LCD_MESSAGEPGM(MSG_STOPPED);
              break;
          }
        }
      }

      // If command was e-stop process now
      if (strcmp(command, "M112") == 0) kill(PSTR(MSG_KILLED));

      cmd_queue_index_w = (cmd_queue_index_w + 1) % BUFSIZE;
      commands_in_queue += 1;

      serial_count = 0; //clear buffer
    }
    else if (serial_char == '\\') {  // Handle escapes
      if (MYSERIAL.available() > 0 && commands_in_queue < BUFSIZE) {
        // if we have one more character, copy it over
        serial_char = MYSERIAL.read();
        command_queue[cmd_queue_index_w][serial_count++] = serial_char;
      }
      // otherwise do nothing
    }
    else { // its not a newline, carriage return or escape char
      if (serial_char == ';') comment_mode = true;
      if (!comment_mode) command_queue[cmd_queue_index_w][serial_count++] = serial_char;
    }
  }

  #if ENABLED(SDSUPPORT)

    if (!card.sdprinting || serial_count) return;

    // '#' stops reading from SD to the buffer prematurely, so procedural macro calls are possible
    // if it occurs, stop_buffering is triggered and the buffer is ran dry.
    // this character _can_ occur in serial com, due to checksums. however, no checksums are used in SD printing

    static bool stop_buffering = false;
    if (commands_in_queue == 0) stop_buffering = false;

    while (!card.eof() && commands_in_queue < BUFSIZE && !stop_buffering) {
      int16_t n = card.get();
      serial_char = (char)n;
      if (serial_char == '\n' || serial_char == '\r' ||
          ((serial_char == '#' || serial_char == ':') && !comment_mode) ||
          serial_count >= (MAX_CMD_SIZE - 1) || n == -1
      ) {
        if (card.eof()) {
          SERIAL_PROTOCOLLNPGM(MSG_FILE_PRINTED);
          print_job_stop_ms = millis();
          char time[30];
          millis_t t = (print_job_stop_ms - print_job_start_ms) / 1000;
          int hours = t / 60 / 60, minutes = (t / 60) % 60;
          sprintf_P(time, PSTR("%i " MSG_END_HOUR " %i " MSG_END_MINUTE), hours, minutes);
          SERIAL_ECHO_START;
          SERIAL_ECHOLN(time);
          lcd_setstatus(time, true);
          card.printingHasFinished();
          card.checkautostart(true);
        }
        if (serial_char == '#') stop_buffering = true;

        if (!serial_count) {
          comment_mode = false; //for new command
          return; //if empty line
        }
        command_queue[cmd_queue_index_w][serial_count] = 0; //terminate string
        // if (!comment_mode) {
        fromsd[cmd_queue_index_w] = true;
        commands_in_queue += 1;
        cmd_queue_index_w = (cmd_queue_index_w + 1) % BUFSIZE;
        // }
        comment_mode = false; //for new command
        serial_count = 0; //clear buffer
      }
      else {
        if (serial_char == ';') comment_mode = true;
        if (!comment_mode) command_queue[cmd_queue_index_w][serial_count++] = serial_char;
      }
    }

  #endif // SDSUPPORT
}

bool code_has_value() {
  int i = 1;
  char c = seen_pointer[i];
  while (c == ' ') c = seen_pointer[++i];
  if (c == '-' || c == '+') c = seen_pointer[++i];
  if (c == '.') c = seen_pointer[++i];
  return (c >= '0' && c <= '9');
}

float code_value() {
  float ret;
  char* e = strchr(seen_pointer, 'E');
  if (e) {
    *e = 0;
    ret = strtod(seen_pointer + 1, NULL);
    *e = 'E';
  }
  else
    ret = strtod(seen_pointer + 1, NULL);
  return ret;
}

long code_value_long() { return strtol(seen_pointer + 1, NULL, 10); }

int16_t code_value_short() { return (int16_t)strtol(seen_pointer + 1, NULL, 10); }

bool code_seen(char code) {
  seen_pointer = strchr(current_command_args, code);
  return (seen_pointer != NULL); // Return TRUE if the code-letter was found
}

#define DEFINE_PGM_READ_ANY(type, reader)       \
  static inline type pgm_read_any(const type *p)  \
  { return pgm_read_##reader##_near(p); }

DEFINE_PGM_READ_ANY(float,       float);
DEFINE_PGM_READ_ANY(signed char, byte);

#define XYZ_CONSTS_FROM_CONFIG(type, array, CONFIG) \
  static const PROGMEM type array##_P[3] =        \
      { X_##CONFIG, Y_##CONFIG, Z_##CONFIG };     \
  static inline type array(int axis)          \
  { return pgm_read_any(&array##_P[axis]); }

XYZ_CONSTS_FROM_CONFIG(float, base_min_pos,   MIN_POS);
XYZ_CONSTS_FROM_CONFIG(float, base_max_pos,   MAX_POS);
XYZ_CONSTS_FROM_CONFIG(float, base_home_pos,  HOME_POS);
XYZ_CONSTS_FROM_CONFIG(float, max_length,     MAX_LENGTH);
XYZ_CONSTS_FROM_CONFIG(float, home_bump_mm,   HOME_BUMP_MM);
XYZ_CONSTS_FROM_CONFIG(signed char, home_dir, HOME_DIR);
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

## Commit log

2016-02-11 Marlin 1.1RC3 for makerfarm pegasus
    [Configuration.h, Configuration_adv.h, shroud.stl]
2016-02-11 added new mods
    mostly planning
    [BoardHolder-diff-led-dual.scad, BoardHolder-diff-led-mini.scad, BoardHolder-diff-led.scad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]
2016-03-18 adding extruder mixing
    [Configuration.h, WadeHerringboneGears.scad, WadeHerringboneGears.stl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]

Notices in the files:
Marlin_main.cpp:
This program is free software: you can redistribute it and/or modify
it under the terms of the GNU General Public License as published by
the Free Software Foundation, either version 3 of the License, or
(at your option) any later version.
